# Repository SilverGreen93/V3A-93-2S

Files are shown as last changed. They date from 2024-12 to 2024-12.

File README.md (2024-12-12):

# Tramvaiul V3A-93-2S

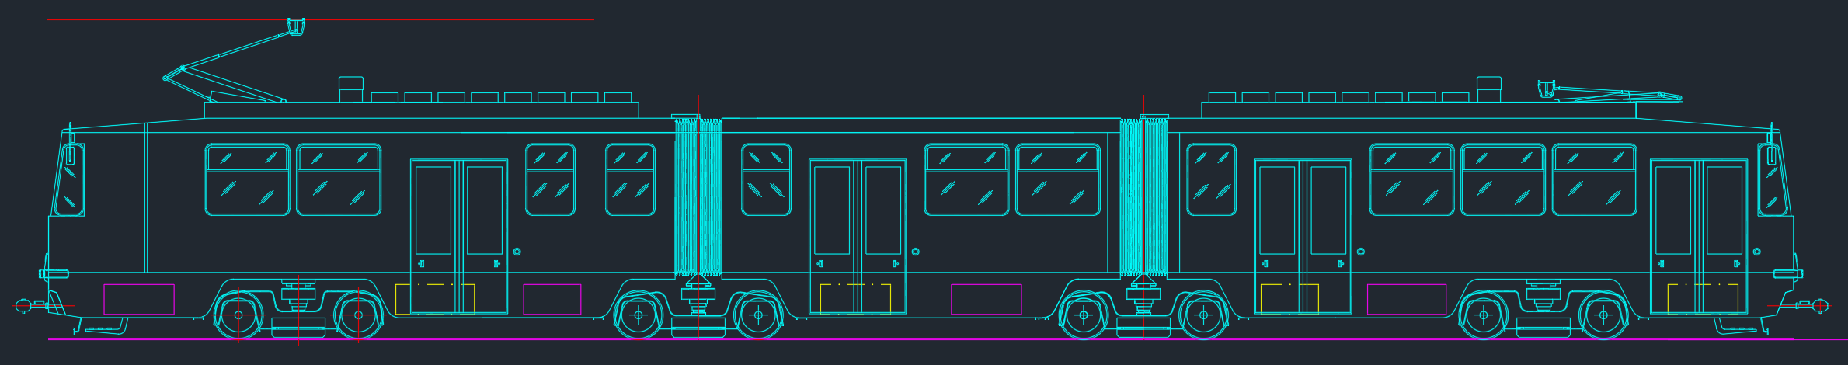
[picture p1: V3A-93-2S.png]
Diagramă V3A-93-2S


Acest repository conține schemele electrice ale tramvaiului românesc bucureștean bidirecțional V3A-93-2S, realizate la RATB - URAC (Regia Autonomă de Transport București - Uzinele de Reprarații Atelierele Centrale) în iulie 2006 de către inginerul proiectant Vasile Dănciulescu.

Schemele se prezintă în formatul original DWG (AutoCAD 2002), dar au fost convertite și în format DXF pentru a putea fi deschide în LibreCAD sau LibreOffice Draw.

De asemenea pentru o vizualizare pe orice dispozitiv sau posibilitate de imprimare imediată, le găsiți disponibile și în format portabil PDF.

# Structură

Găsiți împărțite pe dosare diferite schemele grupate din punct de vedere logic.

Punctul de pornire îl reprezintă dosarul [DOCUMENTATIE](DOCUMENTATIE) unde puteți consulta Memoriul de prezentare și Standardul de firmă (fișa tehnică detaliată a tramvaiului) în format document Word 2003 (original doc, convertit la docx).

Al doilea punct de interes esențial este dosarul [SCHEME](SCHEME), unde se prezintă schemele specifice fiecărui sistem electric al tramvaiului.

Diagrama tramvaiului și bordul cabinei de conducere sînt prezentate în dosarul [PANOURI APARATE](PANOURI%20APARATE).

# Mulțumiri

Mulțumesc pe această cale domnului inginer Vasile Dănciulescu pentru punerea la dispoziția mea pentru publicare aceste scheme ce conțin informații utile pentru istoria transportului bucureștean și oricărui pasionat care dorește răspunsuri tehnice la anumite subansamble ale tramvaielor produse la URAC.

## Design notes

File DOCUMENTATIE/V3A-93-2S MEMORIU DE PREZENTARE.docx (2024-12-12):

### RATB-URAC

### MEMORIU

### DE

### PREZENTARE

### VAGON DE TRAMVAI

### TIP V3A-93-2S

### IULIE 2006

### 1. DENUMIRE PRODUS

Vagon de tramvai articulat V3A-93-2S

### 2. DESCRIEREA PRODUSULUI

2.1 Generalităţi

Vagonul modernizat V3A-93-2S este rezultatul aplicării soluţiilor de modernizare de la proiectul V3A-93 adaptate la vagonul V3A-2S care este un vagon bidirecţional (cu două posturi de conducere şi uşi pe ambele părţi). Acest tip de vagon este necesar pentru deservirea traseelor care nu permit bucle de întoarcere la capete, sau pentru porţiuni de trasee aflate în construcţie.

Aspectul interior al salonului de pasageri a fost îmbunătăţit prin organizarea iluminatului fluorescent, îmbrăcămintea interioară a vagonului se realizează cu plăci care nu sunt higroscopice, rezistente la zgârâieturi, variaţii de temperatură, vibraţii mecanice, având o bună durabilitate.

Vagoanele sunt echipate cu scaune pentru călători montate în consolă şi realizate din materiale rezistente, cu proprietăţi antivandalism şi uşor lavabile.

Indicatoarele de traseu, uşor lizibile, uşurează informarea călătorilor, iar pentru comunicarea conducătorului de vehicul cu aceştia, este prevăzută o instalaşie de de anunţare automată.

Microclimatul vagonului este îmbunătăţit prin montarea pe tronsoanele A şi B a câte unui ventilator. Funcţionarea acestora este, funcţie de sensul de mers, cu introducerea aerului în vagon pe tronsonul A şi scoaterea acestuia pe tronsonul B. Salonul de pasageri este dotat cu elemente rezistive montate pe pereţiilaterali şi două aeroterme prevăzute cu termostat individual.

Uşile cu mişcare plan-paralelă, cu deschidere în exteriorul vagonului, determină o utilizare maximă a spaţiului din zona acceselor. Ele pot fi comandate direct de pasageri, iar automatizarea acestora asigură protecţia pasagerilor contra strângerii la închidere, în conformitate cu normativele internaţionale. Uşile sunt prevăzute cu geamuri lipite.

Pentru creşterea fiabilităţii în ansamblu s-au avut în vedere atât soluţii tehnice la subansamblele care au prezentat defecţiuni sistematice, mergându-se la reproiectare, cât şi măsuri tehnologice.

Din punct de vedere al caracteristicilor tehnice generale de siguranţa circulaţiei, vagonul V3A-93-2S se încadrează atât în condiţiile standardului de firmă cât şi în prevederile codului rutier.

2.2 Descrierea generală a vagonului

Vagonul de tramvai V3A-93-2S are la bază documentaţia de execuţie APUPS şi SPC-URAC.

Vagonul de tramvai V3A-93-2S este un vagon de tramvai dublu articulat format din trei tronsoane:
A – Tronsonul din faţă – cu cabina de conducere

C – Tronsonul din mijloc

B – Tronsonul din spate – cu cealaltă cabină de conducere

Vagonul de tramvai este echipat cu patru boghiuri, două boghiuri motoare şi două boghiuri purtătoare. Boghiurile purtătoare sunt dispuse sub articulaţiile vagonului. Caroseria vagonului se sprijină pe bighiuri prin intermediul rulmenţilor fixaţi pe traverse osclante,

Atât boghiurile motoare cât şi boghiurile purtătoare sunt de tip cu două osii, cu două trepte de suspensie şi cu patine electromagnetice.

Boghiurile motoare sunt prevăzute pe ambele osii cusisteme de frână disc, acţionate de dispozitive cu resort de acumulare.

Boghiul purtător dintre tronsoanele B şi C ale vagonului este prevăzut pe ambele osii cu sisteme de frână disc acţionate de un solenoid.

Boghiurile motoare au motorul de tracţiune dispus longitudinal, care antrenează două reductoare cu angrenaje conice flanşate pe scuturile acestuia. Întregul ansamblu motor-reductor este suspendat faţă de rama boghiului şi este cuplat cu osiile prin intermediul unor cuple cu elemente elastice.

Rama boghiului este de tip H construcţie cheson realizată din tablă OL44-2k asamblată prin sudură.

Trenurile de roţi folosesc roţi elastice. Osia montată este prevăzută cu disc de frână şi semicuplă pentru transmiterea momentului de tracţiune (la boghiurile motoare).

Contactul de punere la pământ este de tip radial. Carcasa contactului de punere la pământ se fixează pe cutia de unsoare.

Boghiurile sunt prevăzute cu două trepte de suspensie. Suspensia primară între osia montată şi rama boghiului este de tipul metal-cauciuc (arcuri Megy),

Pe cutia de unsoare mai sunt montate tampoane de cauciuc care preiau suprasarcinile accidentale.

Suspensia secundară este dispusă între rama boghiului şi traversa oscilantă şi este tot de tipul metal-cauciuc (arcuri Contitech).

Traversa oscilantăeste o construcţie metalică tip cheson executată din tablă OL44, asamblată prin sudură.

Patina electromagnetică de frână este montată suspendat pe cutia de unsoare pentru a asigura păstrarea distanţei între şină şi patină independent de flexiunea suspensiei primare a boghiului.

Vagonul de tramvai este prevăzut cu patru sisteme independente de frânare. Vagonul dispune de frână reostatică, frână cu patină la şină, frână cu solenoid, frână cu resort de acumulare.

Sistemele de frână sunt independente, astfel încât defectarea unuia nu se transmite şi celorlalte.

Frâna de serviciu (reostatică) acţionează numai asupra roţilor motoare. În circuitu frânei de serviciu nu există siguranţe electrice. Viteza minimă până la care frâna reostatică îşi păstreză eficacitatea este de 10 km/h. Simultan cu frâna reostatică, în cadrul frânării cu frâna de serviciu, funcţionează frîna cu solenoid. Frâna cu solenoid se montează pe boghiul purtător B-C şi este eficace tot până la viteza de 10 km/h.

Pentru oprirea vagonului la punct fix, sub viteza de 10 km/h, vor acţiona dispozitivele cu resort de acumulare, dispuse pe boghiurile motoare cu acţionare pe discurile de frână fixate pe osiile motoare. În cazul în care unul dintre dispozitivele cu resort de acumulare se defectează, acesta se poate izola cu ajutorul mecanismului montat pe boghiurile motoare pentru fiecare frână cu resort.

Pentru oprirea vagonului la punct fix se poate folosi şi frâna cu patină electromagnetică, la şină.

Frâna de staţionare compusă din dispozitivele cu resort de acumulare asigură staţionarea în rampă de 60‰ a vagonului încărcat cu 20 t.

Frâna cu patină la şină este independentă de aderenţa dintre roată şi şină, ea se aplică simultan cu frâna de serviciu. Frâna de urgenţă se realilează prin funcţionarea simultană a frânei de serviciu şi a frânei cu patină la şină.

Caroseria tronsoanelor vagonului de tramvai este de tipul semiautoprtantă, confecţionată din profile din oţel ambutisate, are învelişul exterior din tablă fixată în sudură pe schelet, participând în acest fel ca element de rezistenţă. Acoperişul vagonului este realizat din tablă sudată pe cintrele scheletului şi pe elementele de legătură ale acestora.

Pentru protecţia tamponării tronsoanele A şi B au fost protejate cu un blindaj frontal. Structura metalică a vagonului este protejată anticoroziv prin vopsire la exterior, iar la interior antifonic.

Postul de conducere al vagonului de tramvai are o uşă care separă postul de conducere de spaţiul ocupat de pasageri.

În cabina de conducere sunt amplasate: scaunul conducătorului de tramvai (prevăzut cu sistem de reglare pe verticală şi faţă-spate), panoul de aparate de bord, controlerul de mers-frână, dulapurile cu echipament electric situate în stânga şi în spate faţă de conducătorul tramvaiului, instalaţia de climatizare şi degivrare a parbrizului, ventilatorul amplasat deasupra scaunului conducătorului, oglinda interioară, radiatorul şi sursa de alimentare a acestuia, staţia de amplificare, pedala de salvare acţionată din cabină şi pedala de vigilenţă, microfonul aşezat pe pupitrul din partea reaptă, programatorul indicatorului de traseu şi difuzorul situate în spatele conducătorului tramvaiului.

Pe exteriorul cabinei se amplasează un ştergător de parbriz, iar pe laterale, două oglinzi retrovizoare amplasate stânga-dreapta, prevăzute cu încălzire.

Sistemul de organizare a postului de conducere asigură manipulantului un câmp de vizibilitate sub un unghi de 130 – 135°.

Organizarea întregii instalaţii electrice şi echipamentul electric al vagonului este următoarea:

- cabină manipulant, care cuprinde dulap panouri cu aparate, pupitrul de comandă cu aparatajul necesar conducerii şi supravegherii mersului, aeroterma pentru încălzirea cabinei, controlerul de mers-frână, pedala de vigilenţă, instalaţia de ventilaţie şi iluminat cabină, instalaţia de sonorizare, ventilator.
- salon, care cuprinde instalaţia de comandă uşi, rezistenţele de încălzire salon pasageri, aeroterme, instalaţia de iluminat salon.
- tronson A, B, C – exterior vagon care cuprinde cutiile de legături motoare ACM, BCM, alte cutii de legături, canalele de cabluri, compartimente aparate vagon A, compartimente aparate vagon B. Pe rama vagon A mai sunt amplasate cutia de rezistenţe punere la pământ, cutia de rezistenţe de preexcitare, iar pe vagonul C, compartimentul sursă statică, compartimentul acumulatori, rezistenţa punere la masă.
- vagon tronson A şi B: pe acoperişul acestora se amplasează pantografele, bateriile de rezistenţe demaraj-frânare, întrerupătorul automat, bobina self, descărcătorul cu rezistenţă variabilă.

2.3 Ansamblul postului de conducere

În cadrul postului de conducere se concentrează elementele de comandă şi control necesare pentru deplasarea în condiţii de deplină siguranţă şi funcţionalitate a vagonului de tramvai.

Postul de conducere este izolat de salonul de pasageri printr-o uşă, ceea ce rează condiţii mai bune pentru conducere.

Amplasarea elementelor de acţionare este ergonomică, în interiorul postului este asigurată o ventilaţie şi o încălzire corespunzătoare, indiferent de condiţiile meteorologice.

2.4 Instalaţia de încălzire şi degivrare post conducere

Pentru realizarea degivrării parbrizului, se foloseşte degivratorul din aeroterma post conducere. Comanda degivrării este realizată de manipulant printr-un buton amplasat pe pupitru.

Încălzirea postului de conducere se face printr-o aerotermă amplasată sub pupitru în partea dreaptă a manipulantului, care are o putere de 3 kW şi este alimentată la 750 Vcc. Comanda se face printr-un buton amplasat pe pupitru.

Aerul este aspirat din cabină printr-o mască şi este dirijat printr-o tubulatură şi gurile de refulare spre parbriz şi spre interiorul cabinei.

2.5 Sistemul de frânare

2.5.1 Generalităţi

Vagonul de tramvai V3A-93-2S este echipat cu patru sisteme de frânare, funcţionând pe principiul “totul electric” şi care asigură oprirea şi staţionarea vagonului în condiţii de deplină securitate pentru transportul urban.

Aceste sisteme permit frânarea normală (sau de serviciu) şi frânarea bruscă (sau de urgenţă).

Cele patru sisteme de frânare sunt:

- Frâna reostatică sau electrodinamică
- Frâna cu solenoid
- Frâna cu resort de acumulare
- Frâna electromagnetică la şină

2.5.2 Frâna reostatică

Frâna reostatică se comandă prin controler, trecând maneta acestuia în zona de frânare şi parcurgând în mod gradat, funcţie de necesităţi, cele 17 trepte de frânare. În aceste condiţii motoarele sunt alimentate pe primele 6 trepte din reţeaua de joasă tensiune în înfăşurările de excitaţie. Motoarele intră în regim de generatoare, debitând separat pe două reostate de frănare, deci o defecţiune pe un circuit nu afectează pe celălalt.

Frânarea reostatică este eficientă până la 10 km/h.

2.5.3 Frâna cu solenoid

După cum s-a arătat, frâna cu solenoid lucrează concomitent cu frâna reostatică, fiind complementară a acesteia.

Pe timpul staţionării, frâna cu solenoid poate fi utilizată ca o frână complementară frânei cu resort de acumulare.

Solenoidul se alimentează la 24 Vcc.

2.5.4 Frâna cu resort de acumulare

Frâna cu resort de acumulare se utilizează pentru oprirea la punct fix a vagonului şi ca frână de staţionare, deoarece forţa de frânare se realizează prin destinderea unor resorturi.

Dispozitivul resortului de acumulare permite pretensionarea hidraulică a acestuia. Comanda frânei se face prin evacuarea uleiului care realizează pretensionarea, iar forţa dezvoltată de resort se transmite prin intermediul unei timonerii de frână asupra saboţilor ce presează discul de frână.

Frânarea cu dispozitivele cu resort de acumulare se face fie prin intermediul controlerului, fie prin intermediul comutatorului de pe panoul de bord.

2.5.4 Frâna electromagnetică la şină

Toate sistemele de frâmă descrise depind de limita de aderenţă a roţilor pe calea de rulare. Prin intermediul patinelor electromagnetice la şină, greutatea vagonului este mărită cu cca. 35 t, având ca urmare un efect puternic de frânare.

Toate patinele sunt alimentate la 24 Vcc.

Datprită forţelor mari care se transmit asupra ghidajelor patinelor electromagnetice şi a supratensiunilor de comutaţie, nu se recomandă a se abuza de acest sistem de frânare, el trebuind să rămână un sistem de frână de urgenţă.

3. DOCUMENTAŢIA DE EXECUŢIE

La întocmirea tehnologiei de execuţie s-a ţinut cont de: organizarea fluxurilor tehnologice existente în URAC, de dotarea tehnică a liniilor tehnologice precum şi de structura organizatorică a atelierelor, astfel încât reperele executate să respecte condiţiile tehnice din documentaţia de execuţie.

4. CONDIŢII DE FUNCŢIONARE PRIVIND SECURITATEA, SĂNĂTATEA SAU CALITATEA VIEŢII PERSOANEI

4.1 Condiţii privind securitatea şi sănătatea persoanei

4.1.1 Rezistenţa electrică a legăturilor dintre părţile conductoare accesibile şi masă este mai mică de 5 mΩ.

4.1.2 Rezistenţa electrică dintre punctul de conectare la masă al instalaţiei de 750 V şi şină este mai mică de 5 mΩ.

4.1.3 Rezistenţele de izolaţie sunt mai mari de 10 MΩ în stare rece şi uscată şi mai mari de 2 MΩ în stare umedă.

4.1.4 Vagonul trebuie să reziste unei încercări a rigidităţii dielectrice a izolaţiilor conf. CEI77. Se încearcă rigiditatea dielectrică a izolaţiilor:

- Între circuitele de joasă tensiune şi masă – la 750 V,

- Între instalaţia de 750 V şi masă,

- Între instalaţia de 750 V şi circuitele de joasă tensiune – la 3875 V.

4.1.5 Supratemperaturile maxime admisibile după funcţionarea vagonului încărcat timp de 8 ore la principalele agregate, subansamble şi compartimente trebuie să fie:

- reductor de tracţiune 60°C

- lagăr cutie cap osie 55°C

- motor tracţiune TN71 – colector 65°C

- înfăşurare stator 115°C

- înfăşurare indus 80°C

- compartiment controler 50°C

- compartiment conexiune 30°C

- cabluri în jgheab 30°C

- dulapuri de aparataj 25°C

Vagonul va fi încărcat la 80% din sarcina maximă.

4.1.6 Materialele folosite la execuţia produsului trebuie să fie însoţite de certificate de conformitate şi garanţie emise de furnizor. Pentru principalele materiale utilizate la salonul de călători se vor solicita şi avizele privind comportarea la foc, precum şi cele referitoare la igiena şi protecţia muncii.

4.1.7 Trepte tuturor scărilor sunt acoperite cu material antiderapant.

4.1.8 Treptele fiecărei scări sunt iluminate dacă uşa respectivă este deschisă şi dacă sunt aprinse lanternele de poziţie.

4.1.9 Pe toată podeaua vagonului este lipit cu răsfrângere pe pereţii laterali un covor antiderapant.

4.1.10 Pe acoperişul tronsoanelor A şi B, pe ambele laterale, în dreptul rezistenţelor de frânare şi a întrerupătorului untrarapid, există pasarele acoperite ccu tablă striată de aluminiu.

4.1.11 Dacă vagonul nu staţionează, eliberarea pedalei de vigilenţă va declanşa automat frânarea vagonului.

4.1.12 Grătarul salvării cade pe şină dacă asupra declanşatorului frontal este aplicată o forţă normală dinspre exterior.

4.1.13 În salonul pasagerilor sunt amplasate cel puţin etichetele cu inscripţionări de securitate din tabelu 1.

Tabelul 1

Nr. crt. | Dimensiuni (mm) | Text | Poziţia de amplasare
1 | 200x45 | ÎN TIMPUL MERSULUI VĂ RUGĂM SĂ VĂ ŢINEŢI DE BARE | Pe mijloacele capacelor fixe
2 | 85x85 | ÎN CAZ DE PERICOL ROTIŢI MÂNERUL ÎN JOS ŞI DESCHIDEŢI MANUAL UŞA. ABUZUL SE PEDEPSEŞTE | Pe lateralul cutiilor cu aparataj ale uşilor, alături de mânerul de acţionare
3 | 200x100 | ÎN TIMPUL MERSULUI ESTE INTERZIS CĂLĂTORILOR SĂ STEA DE VORBĂ CU CONDUCĂTORUL VEHICULULUI | În spatele posturilor de conducere
4 | 80x50 | FRÂNĂ DE UTGENŢĂ. ABUZUL SE PEDEPSEŞTE | Pe lateralul cutiilor de aparataj ale uşilor, alături de butonul de acţionare
5 | 150x50 | NU VĂ SPRIJINIŢI DE UŞĂ. UŞA SE ÎNCHIDE AUTOMAT | Pe rama superioară a uşii, lizibil din interior
6 | 120x45 | FUMATU INTERZIS | În colţul geamurilor fixe, lizibil din interior
7 | 150x25 | NU VĂ SPRIJINIŢI DE ELEMENTELE ARTICULAŢIEI | Pe fiecare stâlp de articulaţie la înălţimea de 1800 mm
8 | 80x80 | fulger (semnul de indicare a pericolului de electrocutare) ATENŢIE 750 V ! | În centru capacelor izolante indicate

4.2 Condiţii privind calitatea vieţii persoanei

4.2.1 Materialul cu care se realizează îmbrăcămintea interioară a pereţilor şi a plafonului este sub formă de plăci cu următoarele caracteristici minimale:

- culoare uniformă

- rezistenţă la încovoiere prin şoc de min. 42 daN/cm²

- absorbţie apă de max. 0,13 %

- stabilitate dimensionalp până la min. +85°C

- ignifug

Îmbinarea plăcilor este mascată cu ajotorul unor profile de aluminiu.

4.2.2 Pe fiecare tronson, în salonul călătorilor, există rezistenţe de încălzire semiîngropate în pereţi şi acoperite cu capace de protecţie perforate din oţel inoxidabil. Rezistenţele încălzesc salonul dacă butonul “Încălzire salon” este apăsat.

4.2.3 În salonul pasagerilor şi în exteriorul vagonului sunt amplasate cel puţin etichetele cu inscripţionări de dirijare şi orientare din tabelul 2.

Tabelul 2

Nr. crt. | Dimensiuni (mm) | Text | Poziţia de amplasare
1 | 70x80 | DESCHIDERE UŞĂ APĂSAŢI BUTONUL | Pe axa verticală a butonului, deasupra acestuia la 15mm, atât în interior cât şi în exterior
2 | ø70 | Săgeată groasă cu vârful în jos | Pe geamurile uşilor atât în interior cât şi în exterior
3 | ø70 | Bară groasă orizontală | Pe geamurile uşilor atât în interior cât şi în exterior
4 | 160x20 | LOCURI REZERVATE | Pe peretele interior, la mijlocul intervalului dintre primele două scaune dinspre postul de conducere, la 15mm sub profilul de avial
5 | 120x80 | Săgeată groasă cu vârful în jos | La partea superioară a fiecărei bare pe care este montat un validator de tichete

4.2.4 Instalaţia de audioamplificare a vagonului care cuprinde un amplificator şi un microfon în postul de conducere şi o reţea de difuzoare montate în tavan, care trebuie să poată asigura un nivel sonor de cca. 60 dB(A).

5. MĂSURI DE PROTECŢIE A MUNCII ŞI A MEDIULUI

În procesul de fabricaţie al vagonului V3A-93-2S, sunt respectate următoarele norme:

- Instrucţiuni proprii de protecţia muncii pentru întreţinerea şi repararea tramvaielor şi troleibuzelor RATB-1997
- Norme specifice de securitate a muncii pentru construcţii şi confecţii metalice nr. 42/1999
- Norme specifice de securitate a muncii pentru prelucrarea metalelor prin aşchiere nr. 1/1997
- Norme specifice de securitate a muncii pentru sudarea şi tăierea metalelor nr. 1/1997
- Norme specifice de protecţia muncii pentru activităţi de vopsire nr. 26/1996.
- Legea protecţiei muncii nr. 90/1996 şi norme metodologice de aplicare
- Norme generale de protecţia muncii – 1996
- Norme specifice de protecţia muncii pentru transportul şi distribuţia energiei electrice nr. 65/1997
- Norme specifice de securitate a muncii pentru lucrul la înălţime nr. 12/1995
- Instrucţiuni de exploatare pentru proiectarea, construirea, montarea, exploatarea şi verificarea macaralelor, mecanismelor de ridicat şi dispozitivelor auxiliare “R1/1987”.

6. MONTARE, REGULI DE SECURITATE ŞI FOLOSIRE ÎN EXPLOATARE

În conformitate cu documentaţia de execuţie, în realizarea şi exploatarea produsului sunt îndeplinite:

- montarea este în conformitate cu documentaşia emisă de proiectant,
- securitatea şi utilizarea în exploatare au la bază:
  - protecţia călătorilor contra electrocutării şi atingerii instalaţiei electrice sub tensiune prin amplasarea echipamentului electric în compartimente speciale, protejate cu uşi şi capace prevăzute cu închizători,
  - protecţia contra incendiilor prin utilizarea de cablaje cu proprietăţi ignifuge şi realizarea instalaţiei de stins incendiu din compartimentele expuse incendiului,
  - asigurarea siguranţei circulaţiei prin menţinerea stării tehnice corespunzătoare, permanent a vagonului,
- Instrucţiunile de exploatare elaborate, conţin:
  - pregătirea vagonului pentru cursă,
  - pornirea vagonului şi conducerea acestuia în regim economic,
  - frânarea şi oprirea vagonului,
  - staţionarea vagonului,
  - defecte posibile şi modul de rezolvare în traseu,
  - remorcare tramvai defect,
  - măsuri pentru asigurarea siguranţei circulaţiei în situaţii speciale în exploatare,
  - măsuri de protecţia muncii şi PSI pentru conducătorul de tramvai.

MEMORIU DE PREZENTARE MP-V3A-93-2S Data intrării în vigoare 2006 VAGON DE TRAMVAI TIP V3A-93-2S Revizie finală Fila 11/11

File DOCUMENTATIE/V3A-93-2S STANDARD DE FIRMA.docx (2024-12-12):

APROBAT

DIRECTOR TEHNIC MATERIAL RULANT

ing. IORDACHE ŞTEFAN

### 1. GENERALITĂŢI

1.1 Obiectul standardului de firmă

1.1.1 Prezentul standard de firmă se referă la vagoanele de tramvai tip V3A-93-2S, respectiv vagoane cu doua sensuri, modernizate, destinate transportului urban de călători la suprafaţă şi subteran.

1.2 Domeniul de utilizare

Prevederile prezentului standard de firmă se aplică vagoanelor de tramvai tip V3A-93-2S având la bază documentaţia de execuţie RATB reactualizată de APUPS în colaborare cu SPC-URAC.

1.3 Documente de referinţă

- Norme de circulaţie pe drumurile publice;
- Regulamentul de exploatare tehnică a tramvaielor, Ordinul 92/1975-CPCP (RET);
- SR 13342:1996 Transport public urban de călători. Parametrii tehnici;
- BOStrab Bracking Regulations (Regulamentul de frânare BOStrab) 1988;
- Norme - Instrucţiuni tehnice departamentale pentru proiectarea şi construcţia liniilor de tramvai, cod PD164-82;
- CEI 77 Norme care se aplică aparatajului electric de tracţiune;
- STAS 9364/2-91 Vehicule rutiere. Ştergătoare de parbriz. Condiţii generale de calitate;
- STAS 6926/1-90 Autovehicule. Metode de încercare;
- SR ISO 3469:1995 Autoturisme. Sisteme de spălare a parbrizului. Metode de încercare;
- SR HD 405.1 S1:1993 Încercări ale cablurilor electrice supuse la foc. Partea 1: Încercare efectuată pe un cablu vertical;
- SR CEI 332-3:1993 Încercări ale cablurilor electrice supuse la foc. Partea 3: Încercări pe mănunchiuri de cabluri;
- Fişa UIC 564-2;
- STAS 9051/11-75 Suporturi textile acoperite cu elastomeri sau materiale plastice. Comportarea la flacără. Clasificare şi metode de încercare;
- STAS 12321-85 Materiale plastice. Determinarea combustibilităţii prin metoda indicelui de oxigen;
- DIN 51130D;
- STR 680-88-MTTc;
- STAS 6926/7-88 Vehicule rutiere. Etanşarea cabinei şi caroseriei la gaze şi apă. Metode de încercare;
- STAS 8393/5-81 Încercări climatice şi mecanice. Încercarea la căldură umedă ciclică, ciclul de 12+12 h. Metoda de încercare Db;
- STAS 7222-90 Acoperiri metalice. Acoperiri electrochimice de zinc sau cadmiu. Condiţii tehnice de calitate;
- STAS 7043/1-93 Acoperiri nemetalice (anorganice). Acoperiri prin oxidare anodică a aluminiului şi a aliajelor de aluminiu. Condiţii tehnice de calitate;
- STAS 2700/8-82 Organe de asamblare filetate. Caracteristici şi metode de verificare pentru acoperiri de protecţie;
- SR EN ISO 2178:1998 Acoperiri metalice. Determinarea grosimii stratului prin metoda magnetică;
- STAS 6854-90 Acoperiri metalice. Determinarea grosimii stratului prin metoda cu picături;
- Procese tehnologice RT1, RT2 pentru vagoanele modernizate V3-93, proiect SPC nr 3710-1996;
- SR ISO 2808:1993 Vopsele şi lacuri. Determinarea grosimii peliculei;
- SR CEI 60349:1999 Maşini electrice rotative pentru vehicule pe şine şi rutiere;
- CEI - 1133:1992 Traction electrique - Materiel roulant;
- STAS 2172/2-84 Piese de oţel forjate liber. Adaosuri de prelucrare şi abateri limită pentru piese forjate pe ciocane;
- SR ISO 8062/1995 Piese turnate. Sistem de toleranţe dimensionale şi adaosuri de prelucrare;
- STAS 8499/1987 Vehicule rutiere. Frânarea. Terminologie

1.4 Terminologie

In înţelesul prezentului standard de firmă, următoarele noţiuni au semnificaţiile:

1.4.1 Echipament de frânare - ansamblu de dispozitive de frânare care echipează un vehicul şi care are funcţia de a micşora sau de a anula viteza unui vehicul în mers, sau de a-l menţine imobil dacă este oprit.

1.4.2 Dispozitiv de frânare de serviciu - ansamblu de elemente care permit conducătorului să micşoreze, sau să anuleze, direct sau indirect, viteza unui vehicul în timpul conducerii sale normale. Acţiunea sa este variabilă.

1.4.3 Dispozitiv de frânare de securitate (de urgenţă) - ansamblu de elemente care permit conducătorului să micşoreze, sau să anuleze, direct sau indirect, viteza unui vehicul,suplimentar frânei de serviciu si independent de aderenta roata-sina in cazul materialului rulant. Acţiunea sa este variabilă.

1.4.4 Dispozitiv de frânare de staţionare - ansamblu de elemente care permit menţinerea în mod mecanic a unui vehicul imobil, chiar pe un teren înclinat sau în absenţa conducătorului.

1.4.5 Frânare de serviciu - frânarea până la viteza dorită sau până la oprirea vagonului fără punerea în pericol a ocupanţilor vehiculului (conform "Regulamentului de frânare BOStrab).

1.4.6 Frânare de urgenţă - frânare comandată de către conducător dacă apare un pericol în afara vagonului; frânarea poate duce până la oprire; în timpul frânării apar deceleraţii crescute şi smucituri;

1.4.7 Frânare de staţionare - frânare utilizată pentru prevenirea plecării de pe loc a vehiculului (conform "Regulamentului de frânare BOStrab).

1.4.8 Iluminatul normal - funcţionarea iluminatului salonului cu tuburi fluorescente alimentate din tensiunea furnizată de sursă în tampon cu bateria de acumulatori la tensiunea de 24 V.c.c. ±20%.

1.4.9 Iluminatul de siguranţă - funcţionarea iluminatului din bateria de acumulatori de 24 V.c.c. cu becuri incandescente în cazul lipsei tensiunii furnizate de sursa statică

1.4.10 Circuite de joasă tensiune - circuite cu tensiunea nominală de alimentare 24 V.c.c.

1.4.11 Circuite de înaltă tensiune - circuite cu tensiunea nominală de alimentare de 750 V.c.c.

1.4.12 Fază scurtă - lumină de întâlnire

1.4.13 Fază lungă - lumină de drum. Este semnalizată şi la bord (bec martor).

Faza scurtă şi faza lungă sunt condiţionate de aprinderea prealabilă a luminilor de poziţie şi lămpilor de gabarit.

1.4.14 Indicele calităţii de mers - indice de evaluare a confortului călătorilor determinat de componenta dinamică a vehiculului pe cale. Formula determinată experimental a indicelui calităţii de mers este:

Wz =

în care:

Wz - indicele calităţii de mers

T - durata înregistrării valorilor acceleraţiei vibraţiilor

a = a(ν,t) este acceleraţia vibraţiilor în domeniul de frecvenţe (νmin , νmax);

B = B(ν) este un factor de ponderare în frecvenţă pentru acceleraţii, dependent şi de direcţia vibraţiilor.

1.4.15 Mers normal - cu ambele motoare de tracţiune în funcţiune. El se realizeaza în ambele sensuri de mers din posturi de conducere distincte şi pe echipamente şi circuite de tracţiune diferite pentru fiecare sens, cu exceptia motoarelor de tracţiune care sunt aceleaşi. Uşile de acces de pe fiecare parte laterală dreapta pot fi acţionate numai din postul de conducere corespunzător sensului respectiv de mers.

1.4.16 Mers de avarie - cu un motor de tracţiune defect izolat.

Atât mersul normal cat şi cel de avarie nu pot fi acţionate dintr-un post de conducere decât cu condiţia punerii axului inversor al controlerului din celălalt post pe pozitia ZERO şi după asigurarea celorlalte condiţii de mers: inchiderea uşilor, apăsarea pedalei de vigilenţă şi defrânarea vagonului din toate sistemele de frână. Frânarea, deschiderea uşilor, eliberarea pedalei de vigilenţă şi căderea tensiunii din reţea au prioritate în regimul de mers, în sensul că suprimă automat regimul de tracţiune. Tracţiunea nu poate fi reluată decât după readucerea controlerului (axul principal mers-frână) pe poziţia ZERO şi refacerea celorlalte condiţii de mers.

1.4.17 Exploatarea normală - în conformitate cu "Regulamentul de exploatare tehnică a tramvaielor" aprobat de CPCP.

1.4.18 Frâna cu patină la şină – sistem care asigură frânarea independent de coeficientul de frecare dintre roată şi şină.

1.4.19 Frâna cu solenoid – asigură frânarea vagonului simultan cu frânarea reostatică (realizată de motoarele de tracţiune numai pe boghiurile motoare) şi acţionează pe boghiul purtător BC. Ea se poate alimenta şi independent din sursa de joasă tensiune.

1.4.20 Grătarul salvării – este un subansamblu al dispozitivului de salvare care este declanşat şi cade la nivelul şinei în momentul atingerii declanşatorului de către un obstacol mai înalt de 140 mm şi care nu permite preluarea acestuia direct de agregatele de rulare.

1.4.21 Declanşatorul frontal al salvării – este un subansamblu al dispozitivului de salvare care la atingerea unui obstacol mai mare de 140 mm aflat între şine declanşează grătarul salvării, care cade la nivelul şinei.

1.4.22 Supratemperatură - prin supratemperatură se va înţelege diferenţa de temperatură între temperatura măsurată şi temperatura mediului ambiant;

1.4.23 Stare caldă - este starea echipamentului electric după două ore de funcţionare corectă (fără incidente, anomalii, etc.);

1.4.24 Post de conducere - este locul din care se face conducerea vehiculului şi se află în partea din faţa a tramvaiului asociată sensului de mers înainte.

1.5 Simbolizare

Vagonul de tramvai dublu articulat, format din 3 tronsoane, este simbolizat prin V3A-93-2S cu următoarele semnificaţii:

- V – vagon
- 3 – nr. tronsoane
- A – articulat
- 93 – varianta constructivă (modernizată)
- 2S – doua sensuri

1.6 Durata de viaţă

Conform Legii 15/1994 durata de utilizare normată este de 14 ani.

1.7 Cerinţe privitoare la mediul înconjurător

- Zona climatică: N (SR HD 478.2.1 S1:2002);
- Categoria de exploatare: 1 (STAS 6692-83);
- Domeniul temperaturilor de utilizare: -33...+55 oC;
- Umiditatea relativă medie lunară în perioada cea mai caldă şi umedă raportată la +20 oC: 90% timp de două luni;
- Altitudinea maximă de utilizare: 1200 m;
- Viteza maximă a vântului: 140 km/h;
- Atmosferă neexplozivă;
- Agenţi exteriori: ploaie, ceaţă, praf, noroi, zăpadă, chiciură, gheaţă, soluţie salină;
- Înălţimea maximă a apei peste nivelul superior al şinei: 50 mm;

1.8 Cerinţe constructive, funcţionale şi de altă natură

1.8.1 Cerinţe constructive

Cotele de gabarit şi funcţionale ale vagonului V3A-93 sunt reprezentate în anexa 1.

1.8.2 Cerinţe funcţionale

Vagoanele de tramvai sunt destinate să funcţioneze:

- în traficul urban
- viteza maximă 55 km/h
- raza minimă de înscriere în curbă 18 m
- aliniament obligatoriu în curbe S cu raza de 18 m 7 m
- raza curbei S fără aliniament 30 m
- raza minimă de mers în covată 800 m
- raza minimă de mers pe cocoaşă 800 m
- calea de rulare şi reţeaua de contact trebuie să fie executate conform “Normelor – Instrucţiuni tehnice departamentale pentru proiectarea şi construcţia liniilor de tramvai” cod PD 164 – 82, pentru a fi asigurate condiţiile de siguranţă a circulaţiei
- în vagoane formate din 3 tronsoane articulate
- rampa maximă 60 ‰
- ecartament linie: 1435 mm;
- Valorile maxime ale acceleraţiilor vibraţiilor determinate de calea de rulare:

- 8 g pentru capul osiei;

- 1 g pentru caroserie;

- 3 g pentru rama boghiului;

- 2 g pentru motorul electric de tracţiune;

- Tensiunea reţelei de contact: 750 Vcc.

1.9 Descrierea şi funcţionarea produsului

1.9.1 Vagoanele de tramvai sunt realizate din 3 tronsoane legate între ele, notate în ordinea:

A – tronsonul din faţă – cu cabina conducătorului de tramvai

B – tronsonul din spate – cu cealaltă cabină de conducere.

C – tronsonul din mijloc

Zona articulaţiei dintre două tronsoane este alcătuită din jug, podea de articulaţie, burdufuri, articulaţiile propriu-zise şi amenajarea interioară de protecţie pentru călători. Tronsoanele sunt asigurate împotriva desprinderii în situaţii de deraiere.

1.9.2 Caroseria tronsoanelor este de tipul semiautoportantă, confecţionată din profile de oţel, învelite cu tablă fixată prin sudură, care participă ca element de rezistenţă.

Acoperişul este realizat din elemente de legătură longitudinale şi transversale pe care se sudează tablă. Pentru protecţia la tamponări, tronsoanele A şi B au fost protejate cu un blindaj frontal.

1.9.3 Caroseria vagoanelor este protejată anticoroziv prin grunduire, vopsire şi antifonare.

1.9.4 Vagonul dublu articulat V3A-93-2S este echipat cu 4 boghiuri, dintre care 2 motoare şi 2 purtătoare. Boghiurile purtătoare sunt dispuse sub articulaţii. Boghiurile sunt prevăzute cu două tipuri de suspensie. Suspensia primară între osia montată şi rama boghiului şi suspensia secundară între rama boghiului şi caroseria vagonului. Suspensia primară este realizată cu resorturi de cauciuc tip MEGY iar suspensia secundară este cu resort de cauciuc tip Contitech.

Rama boghiurilor este de tip H construcţie cheson realizată din tablă OL44 2k asamblată prin sudură.

Fiecare boghiu motor este echipat cu un motor de tracţiune aşezat longitudinal faţă de sensul de deplasare al vagonului, acţionând prin intermediul a două reductoare asupra celor două osii şi de aici asupra roţilor elastice. Transmisia între reductor şi osie se realizează printr-un cuplaj elastic.

Legătura dintre boghiu şi caroserie se realizează prin intermediul unei traverse cu rulment de crapodină.

1.9.5 Vagoanele de tramvai sunt prevăzute cu 4 sisteme independente de frânare. Vagonul dispune de frână reostatică, frână cu patină la şină, frână cu solenoid şi frână cu resort de acumulare.

Frânele vagonului asigură oprirea în limitele şi condiţiile cuprinse la cap. 2. Sistemele de frânare sunt independente, încât defectarea unuia nu se transmite şi la celelalte. Frâna reostatică acţionează numai asupra roţilor motoare şi asigură o frânare la limita blocării roţilor. Forţa de frânare este realizată în trepte de frânare prin intermediul controlerului de bord. În circuitul frânei de serviciu nu există siguranţe electrice.

Viteza minimă până la care frâna reostatică îşi păstrează eficacitatea este de cca. 10 km/h.

Simultan cu frânarea reostatică, în cadrul frânării cu frâna de serviciu funcţionează frâna cu solenoid. Frâna cu solenoid este eficace tot până la viteza de circa 10 km/h. Pentru oprirea vagonului la punct fix sub viteza de 10 km/h se acţionează dispozitivele cu resort de acumulare dispuse pe boghiurile motoare cu acţionare pe discurile de frână fixate pe osiile motoare şi în plus se poate folosi şi frâna cu patină electromagnetică la şină.

Frâna de staţionare compusă din sistem cu resort de acumulare cu acţionare hidraulică HK asigură staţionarea în rampa de 60 ⁰/00 a vagonului încărcat cu 20 t.

Frâna cu patină la şină este independentă de aderenţa dintre roată şi şină. Ea se poate aplica simultan cu frâna de serviciu.

Frâna de urgenţă se realizează prin funcţionarea simultană a frânei de serviciu şi a frânei cu patină la şină.

1.9.6 Echipamentul electric de pe vagon se împarte în:

- Echipament electric de “înaltă tensiune”, valoarea nominală a înaltei tensiuni fiind 750 V.c.c.

- Echipament electric de “joasă tensiune”, valoarea nominală a joasei tensiuni fiind 24 V.c.c. ±20%

###### 1.9.6.1 Instalaţiile şi echipamentele electrice sunt protejate împotriva scurtcircuitelor, suprasarcinilor şi supratensiunilor accidentale, exceptând cazul frânării reostatice.

###### 1.9.6.2 În conformitate cu normele de circulaţie pe drumurile publice în vigoare, vagoanele de tramvai sunt dotate cu echipamente de iluminat, semnalizare de direcţie, semnalizare acustică, mers înapoi, stop şi altele.

###### 1.9.6.3 Iluminatul interior este asigurat de 26 tuburi fluorescente de 20 W alimentate prin invertoare electronice din sursa de joasă tensiune. Vizibilitatea pe timpul nopţii a conducătorului de vehicul nu este afectată de iluminatul interior.

###### 1.9.6.4 Fiecare casă a scării are amplasate lămpi prevăzute cu becuri de 24 V care se aprind la deschiderea uşilor în perioada când funcţionează lumina de poziţie.

###### 1.9.6.5 Instalaţia de comunicare

###### Vagonul dispune de cate o instalaţie de audioamplificare pentru informarea şi dirijarea călătorilor, din fiecare post de conducere, având câte 5 difuzoare în salon (1/A;2/C;2/B pentru un sens şi 2/A;2/C;1/B pentru celălalt sens) şi câte unul în cabină.

1.9.6.6 Vagonul este dotat cu cate 2 faruri rotunde ELBA prevăzute cu câte un bec de 40 x 45 W, pentru fază scurtă şi respectiv fază lungă şi cu câte un bec de 3 W pentru poziţie, pentru fiecare sens de mers. Pe colţurile părţilor frontale, stânga şi dreapta sunt montate câte 2 semnalizatoare de direcţie, tip A 3 – ELBA cu lumină portocalie, dotată cu un bec de 5 W.

###### Pe tronsoanele A şi B sunt montate, pe părţile laterale, câte două lămpi de semnalizare cu lumină intermitentă portocalie tip LDS, prevăzute cu becuri de 15 W, acţionarea acestora se face prin intermediul unui releu de semnalizare electronic.

Tronsoanele A si B au prevăzute, sub faruri, cate 10 lămpi tip AS1 prevăzute cu dispersor roşu pentru stop, poziţii pe ceaţă cu dispersor alb pentru mersul înapoi, dispersor galben pentru semnalizare direcţie şi avarie, cosiderate ca’ ”lampi spate” pentru fiecare sens de mers. Acestea, ca şi farurile, nu pot fi aprinse dacât conform codului de semnalizare rutieră din postul de conducere corespunzator.

###### Becul pentru stop este de 21 W, cel pentru poziţii şi semnalizare de 10 W, iar cel pentru mers înapoi şi ceaţă este de 15 W.

###### 1.9.6.7 Vagonul este prevăzut cu câte un clopot de semnalizare acustică cu acţionare electrică, pentru fiecare post de conducere. Intensitatea sonoră a clopotului este cuprinsă între 80÷90 dB măsurată în exterior.

###### 1.9.6.8 Protecţia împotriva supratensiunilor atmosferice este realizată cu cate un descărcător catodic cu rezistenţă variabilă, pentru fiecare echipament de tracţiune.

###### Circuitele electrice sunt protejate contra supracurenţilor şi suprasarcinilor prin siguranţe fuzibile sau întrerupătoare automate.

###### Circuitul motoarelor de tracţiune este protejat de câte un întrerupător automat pentru fiecare echipament de tracţiune. Rezistenţa de izolaţie între circuite şi masă este mai mare de 10 MΩ în stare rece şi uscată.

###### 1.9.6.9. Acţionarea vagonului se face cu două motoare de tracţiune de curent continuu. Comanda demarajului şi a frânării de serviciu se face cu ajutorul unui controler acţionat manual din fiecare post de conducere.

###### Regimul de mers normal este cu ambele motoare de tracţiune. În caz de defect se permite funcţionarea temporară cu un singur motor, prin izolarea motorului defect din maneta de comandă a axului inversor al controlerului.

Poziţiile manetei de comandă a axului inversor a controlerului sunt:

- mers înainte motor II
- mers înainte motor I
- mers înainte motor I + II
- zero (repaus)
- mers înapoi motor I + II
- mers înapoi motor I
- mers înapoi motor II

1.9.7 Tronsoanele A si B ale vagonului dispun de câte o cabină a conducătorului de vehicul care este de tipul complet închisă cu uşa de acces în dreptul primei semifoi a uşilor de acces în tramvai. În cabină sunt amplasate: scaunul, prevăzut cu un sistem de reglare pe verticală şi în adâncime – faţă de panoul de aparate al bordului; dulapurile cu echipament electric, situate în stânga şi în spate faţă de conducător; instalaţia de încălzire, ventilaţie şi degivrare a parbrizului.

###### Panoul cu aparate al bordului este prevăzut înclinat la 15° pentru ca razele reflectate să nu jeneze conducătorul.

###### Cabina de conducere este prevăzută cu un parbriz frontal care asigură o vizibilitate a conducătorului cu un unghi de 130 ÷ 135°. Pe parbriz şi geamurile laterale ale postului de conducere este aplicată folie bruxafol. Cabina este dotată cu un ştergător de parbriz şi instalaţie de spălare a acestuia.

###### Cabina are două oglinzi retrovizoare montate în exterior, în dreapta şi în stânga vehiculului, în direcţia de mers, prevăzute cu sistem de încălzire.

###### 1.9.8 Îmbrăcămintea interioară a pereţilor vagoanelor se realizează cu plăci care nu sunt higroscopice, sunt lavabile, rezistente la zgârâeturi, variaţii de temperatură, vibraţii mecanice, având o bună durabilitate în timp. Îmbinarea se face cu profile corespunzătoare fixate de caroserie.

1.9.9 Podeaua este realizată din plăci din material lemnos, impregnate pentru a nu fi higroscopice, aşezate pe şasiu prin intermediul unor cusaci de lemn şi benzi de cauciuc. In salon, pe podea, se amplasează prin lipire un covor de pardoseală realizat din materiale antiuzură, cu proprietăţi ignifuge conform normelor PSI în vigoare.

###### 1.9.10 Vagoanele sunt echipate cu scaune pentru călători, montate în consolă şi realizate din materiale rezistente, cu proprietăţi antivandalism şi uşor lavabile.

###### 1.9.11 În interiorul vagonului de pasageri sunt dispuse pe cele două părţi, bare de susţinere orizontale, amplasate la 1850 mm faţă de nivelul podelei vagonului. Ele sunt confecţionate din ţeavă de oţel, acoperite prin vopsire în câmp electrostatic.

###### 1.9.12 În scopul îndrumării călătorilor, vagoanele sunt prevăzute cu inscripţii indicatoare şi cu difuzoare şi instalaţie de anunţare automată a staţiilor acţionată de conducătorul vehiculului.

În partea exterioară a vagonului se înscriu:

- semne pe uşi cu indicaţia de urcare şi coborâre
- semne pentru marcarea locurilor de defrânare manuală

În partea interioară a vagonului se înscriu:

- locurile destinate pentru invalizi, femei gravide, persoane cu copii în braţe
- alte indicaţii cu privire la comportarea călătorilor
- geamurile folosite ca ieşire de urgenţă în caz de accident.

Pentru spargerea acestor geamuri, vagoanele sunt prevăzute cu ciocane fixate în suporţi şi sigilate.

Inscripţiile trebuie să fie vizibile şi lizibile.

1.9.13 Microclimatul vagonului este asigurat prin următoarele mijloace:

- ventilaţie naturală – ferestre rabatabile; ventilaţii centrale pe acoperiş – una tronsonul A şi una pe tronsonul B;
- ventilaţie forţată – câte un electroventilator pe tronsoanele A şi B care introduc aer în interior.
- Fiecare cabina manipulant este dotată cu aerotermă, ventilator în plafon şi radiator.
- salonul pasageri este dotat cu 12 elemente rezistive montate în pereţii laterali si 2 aeroterme (1/A si 1/B).
- microclimatul din interiorul vagonului este supravegheat prin instalarea unui termostat general.

###### 1.9.14 Pentru îmbunătăţirea aderenţei dintre roată şi cale, vagoanele sunt echipate cu cate 2 nisipare, instalate înaintea primei osii motoare pentru fiecare sens de mers şi pot fi acţionate numai câte doua din fiecare cabină, corespunzator sensului de mers inainte.

###### Nisiparele sunt dotate cu rezistenţe de încălzire şi uscare a nisipului, alimentate la 750 V printr-un circuit separat, protejat cu siguranţă fuzibilă.

###### Comanda nisipării se poate face atât automat simultan cu sistemele frânei de urgenţă, cât şi manual de către manipulant, separat de sistemele de frânare, pentru a se putea realiza demarajul în rampă.

###### 1.9.15 Vagoanele sunt prevăzute sub fiecare cabina a conducătorului cu un dispozitiv de salvare.

###### Salvarea este prevăzută cu un declanşator frontal şi un grătar. În timpul mersului, dacă vagonul şi respectiv declanşatorul frontal atinge un obstacol se declanşează grătarul pentru ca obstacolul să nu poată ajunge sub agregatele de rulare ale vagonului.

Declanşarea salvării se poate realiza şi de conducătorul vehiculului.

###### 1.9.16 Vagoanele au la capete câte un aparat de cuplare.

###### 1.9.17 Pentru identificarea numărului şi a traseului vagoanelor, tramvaiele sunt dotate cu indicatoare de traseu cu LED-uri comandate de cate un controler şi microprocesor instalat în cabinele de conducere:

- unul frontal şi două laterale, care indică traseul şi linia pe care circula, pentru fiecare sens de mers.

###### 1.9.18 Vagoanele au în dotare 6 stingătoare de incendiu cu praf şi CO2, accesibile conducătorului de vehicul, cât şi pasagerilor:

- cate un stingător deserveşte în mod permanent controlerul. Controlerul este prevăzut cu clapete de acces stingător gravitaţionale;
- cate un stingător deserveşte în mod permanent canalul de coborâre cabluri, fiind conectat la acesta prin ţeavă;
- două libere.

1.9.19 Pe acoperişul tronsoanelor A si B, în dreptul boghiurilor motoare este montat cate un pantograf, destinat să asigure captarea curentului de la reţeaua aeriană de contact, şi prevăzut cu înzăvorâre în poziţia coborât pentru fiecare sens de mers. Pantografele sunt de tip asimetric şi sunt utilizate alternativ (numai cel din fata, pentru fiecare sens de mers, celalalt fiind pliat).

###### De asemenea, pe acoperisul tronsoanelor A si B sunt montate câte un set de baterii de rezistente demaraj-franare şi câte un disjunctor cod 5500.

###### 1.9.20 Pentru accesul şi deplasarea personalului de intervenţie, pe acoperişul vagonului s-au prevăzut pasarele de tablă de aluminiu striată.

###### 1.9.21 Vagoanele sunt dotate cu semnale de alarmă la fiecare uşă care comandă frânarea vehiculului prin patine şi solenoid în caz de acţionare, precum şi activarea clopotului.

###### 1.9.22 Vagoanele sunt prevăzute cu instalaţii de siguranţă a circulaţiei şi vigilenţă (pedală de vigilenţă în fiecare cabină). Aceasta, în cazul pierderii capacităţii conducătorului şi neapăsarea pedalei, acţionează frâna de urgenţă a vagonului;

###### 1.9.23 Postul de conducere de pe tronsonul B elimină postul de manevra.

###### 1.9.24 Accesul călătorilor este asigurat prin uşile tip IFE de pe partea dreapta pentru fiecare sens de mers, dispuse astfel:

- tronson A – 2 uşi/dreapta + 1 uşă/stânga
- tronson B – 1 uşă/dreapta + 2 uşi/stânga
- tronson C – 1 uşă/dreapta + 1 uşă/stânga

Uşile 2, 3, şi 4, pentru urcarea pasagerilor, asigură o deschidere de aprox. 1200 mm. Fiecare din cele 4 uşi/sens sunt comandate din cabina conducătorului vagonului, pentru fiecare existând şi un buton de deschidere de către pasageri, atât pe interior cât şi pe exteriorul vehiculului, condiţionat de comanda conducătorul vehiculului. Uşa nr. 1/sens, semifoaia 1, este dotată cu buton de acţionare închidere exterior mascat. Această semifoaie este acţionată separat de celelalte uşi, fiind destinată numai accesului conducătorului de vehicul.

###### 1.9.25 Elementele interioare demontabile ale vagonului şi capacele compartimentelor cu aparate sunt asigurate, încât nu pot fi desfăcute decât de personalul de întreţinere şi de intervenţie. Pe panourile care conţin aparate cu pericol de electrocutare este marcat semnul de tensiune periculoasă.

###### 1.9.26 Principalele caracteristici tehnice şi funcţionale ale vagonului:

- ecartament 1435 mm
- raport de transmisie reductor 1:5,66
- formula osiilor B’2’2’B’
- masa vagonului gol 36,5 t +5%
- masa vagonului încărcat – maxim 53,1 t +5%

(Încărcătura utilă maximă se stabileşte ca fiind 750N/loc pe scaun + 5000N/m² de suprafaţă locuri în picioare – conform BOSTRAB. Aceasta este: Gu=34x750N+27,3m²x5000N=16200daN sau Gu=16510 kgf=16,51 tf.)

- nr. locuri - pe scaune 34
- în total călători 254 (65kg/călător)
- raza minimă de înscriere în curbă 18 m
- aliniament obligatoriu în curbe S cu raza de 18 m - minim 7 m
- raza curbei S fără aliniament minim 30 m
- raza minimă la mersul pe cocoaşă 800 m
- raza minimă la mersul în covată 800 m
- tensiunea de alimentare 750 Vcc
- puterea uniorară specifică 0,87 kW/kN
- acţionare vagon controler
- sisteme de frânare:

a. frână de serviciu -electrodinamică, frână cu resort cu solenoid

b. frână independentă de aderenţa roată–şină, - cu patină la şină

c. frână de staţionare - dispozitive cu resort de

acumulare cu acţionare hidraulică tip HK

- rampa maximă 60 ⁰/00
- viteza maximă 55 km/h
- acceleraţie demaraj 0,8 m/s²
- consum specific de energie fără încălzire cca. 8 Wh/kN km
- lungimea vagonului 27180 mm
- lăţimea vagonului cu uşile închise la înălţimea

de 3,4 m de la şină 2390 mm

- înălţime măsurată de la suprafaţa superioară a şinei la

suprafaţa de contact a pantografului retras 4200 mm

- putere nominală pentru tracţiune 2x120 kW

2. CONDIŢII TEHNICE

2.1 Condiţii de execuţie a reperelor

###### 2.1.1 Materialele, componentele şi subansamblurile utilizate trebuie să fie cele prevăzute în documentaţia de execuţie. Se permite utilizarea unor materiale, componente sau subansambluri cu caracteristici similare sau superioare, cu avizul scris al proiectantului şi beneficiarului.

2.1.2 Materialele folosite la execuţia produsului trebuie să fie însoţite de certificate de conformitate şi garanţie emise de furnizor. Pentru principalele materiale utilizate la salonul de călători se vor solicita şi avizele privind comportarea la foc, precum şi cele referitoare la igiena şi protecţia muncii.

###### 2.1.3 Derogările de la materialele indicate în documentaţie, se acordă pe bază de aviz scris emis numai de către proiectant la solicitarea scrisă a executantului cu avizul beneficiarului conform procedurii derogatorii.

###### 2.1.4 Pentru toate dimensiunile şi cotele neprevăzute cu toleranţe se respectă prevederile SR EN 22768/1:2, clasa de precizie m la toleranţele dimensionale şi s la toleranţele geometrice.

###### 2.1.5 Pentru toate dimensiunile şi cotele neprevăzute cu toleranţe, la piesele executate prin sudare, se vor respecta prevederile STAS 9101/1-89, clasa de precizie B.

###### 2.1.6 Pentru toate dimensiunile şi cotele neprevăzute cu toleranţe, la piesele executate prin turnare şi forjare se admit abateri limită conform STAS 2171/2-84 (piese forjate) şi respectiv SR ISO 8062/1995 (piese turnate).

###### 2.1.7 Derogările de la cotele şi toleranţele indicate în documentaţie se acordă în scris numai de către proiectant.

###### 2.1.8 Pregătirea pieselor pentru sudare şi operaţia de sudare trebuie să se facă în conformitate cu prescripţiile din documentaţia de execuţie.

###### 2.1.9 Echipamentul, agregatele şi componentele ce se achiziţionează, trebuie să fie omologate, în producţia curentă a furnizorului şi însoţite de certificate de conformitate şi garanţie şi avizele privind normele PSI, NPSM şi medicina muncii.

###### 2.1.10 Subansamblurile importante nominalizate în anexa 4 au standarde de firmă sau NTR, la livrare sunt însoţite de fişe de măsurători şi documente de atestare a calităţii conform contractului.

2.2 Condiţii de gabarit

- lungimea la gabaritul cu tampoane montate
- în axul longitudinal al vagonului 27180±150 mm
- lungimea la gabaritul fără tampoane 26180±30mm
- lăţimea măsurată la 1,4 m peste nivelul şinei 2390 ±10 mm
- înălţimea măsurată de la suprafaţa superioară a şinei la suprafaţa de contact a pantografului retras 4200 ±15 mm
- înălţimea salonului de pasageri 2220 ±10 mm
- distanţa între axul căii de rulare şi
- extremităţile oglinzilor retrovizoare 1400 ±10 mm
- garda la sol în stare nouă:

- vagon plin 140 ±10 mm

- vagon gol 160 ±10 mm

- garda la sol cu bandajele uzate la maximum

şi suspensia cu săgeata maximă:

- vagon plin 72 ±10 mm

- vagon gol 92 ±10 mm

- înălţimea în dreptul grătarului salvării (cu posibilitate de reglaj): - vagon plin 140 ±10 mm

- vagon gol 160 ±10 mm

2.3 Condiţii de greutate

###### 2.3.1 Greutatea unui vagon de tramvai gol este de 365 ± 5% kN şi condiţiile pentru încărcările pentru fiecare roată trebuie să corespundă tabelului din ANEXA 6.

###### 2.3.2 Valorile de încărcare a boghiurilor pentru vagonul de tramvai gol sunt: boghiu motor I 11800 daN ±5%

boghiu purtător AC 6450 daN ±5%

boghiu purtător BC 6450 daN ±5%

boghiu motor II 11800 daN ±5%

2.4 Condiţii privind calitatea suspensiei

###### 2.4.1 Vagonul în stare neîncărcată, după reglarea suspensiei traversei oscilante, trebuie să realizeze cota de 870 ± 10 mm între suprafaţa inferioară a structurii metalice a bazei caroseriei şi suprafaţa de rulare, stânga şi dreapta.

###### 2.4.2 În aceleaşi condiţii de la pct. 2.4.1 vagonul trebuie să realizeze pe lungimea sa cota de 870 ± 10 mm (faţă, spate, mijloc).

###### 2.4.3 Vagonul încărcat cu sarcina nominală trebuie să realizeze cota de 850 ± 15 mm între suprafaţa inferioară a bazei vagonului şi suprafaţa de rulare stânga şi dreapta cât şi pe lungimea sa (faţă, spate, mijloc).

    2.4.4 Distanţa dintre cadrul boghiului şi cutia de unsoare, respectiv cota “I”, este:

108 mm – vagon gol

96 mm – vagon încărcat

2.5. Comportarea la vibraţii

Vagonul de tramvai trebuie să funcţioneze în parametri nominali pe o cale de rulare care determină în circulaţie următoarele valori maxime ale vibraţiilor:

- 1 g pentru caroserie
- 3 g pentru rama boghiului
- 2 g pentru motorul de tracţiune
- 8 g pentru capul de osie

2.6 Condiţii pentru nivelul de zgomot admis

###### 2.6.1 Nivelul de zgomot maxim admis în exterior trebuie să se situeze la o valoare de 85 dB(A).

###### 2.6.2 Nivelul de zgomot maxim admis în interiorul salonului de pasageri trebuie să se situeze la o valoare de 80 dB(A).

###### 2.6.3 Nivelul de zgomot maxim admis în interiorul cabinei conducătorului de vehicul trebuie să se situeze la o valoare de 76 dBA, cu excepţia zgomotului produs de controler.

2.7 Rezistenţele de izolaţie

###### 2.7.1 Rezistenţele de izolaţie trebuie să fie mai mari de 10 MΩ în stare rece şi uscată, valori impuse în fişa de măsurători nr. 2.

###### 2.7.2 Rezistenţele de izolaţie trebuie să fie de 2 MΩ în stare umedă şi caldă. Proba de determinare a rezistenţei de izolaţie în stare umedă şi caldă este probă de investigaţie.

2.8 Valorile rezistenţelor electrice ale circuitelor de tracţiune şi auxiliare nu trebuie să se abată cu mai mult de ±20% faţă de valorile nominale înscrise în fişa de măsurători nr. 3.

2.9 Părţile conducătoare care nu sunt cale de curent sunt legate la masa vagonului prin legături de împământare. Rezistenţa electrică a unei legături de împământare este de cel mult 0,030 Ω în stare nouă.

2.10 Verificarea rigidităţii dielectrice conform CEI 77

La circuitele care lucrează la 750 Vcc, la aplicarea unei tensiuni de încercare de 3875 Vca 50Hz timp de 1 min., nu trebuie să apară străpungeri sau conturnări.

La circuitele care lucrează la 24 Vcc, la aplicarea unei tensiuni de încărcare de 750 Vca 50 Hz timp de 1 min., nu trebuie să apară străpungeri sau conturnări.

Punctele de aplicare sunt precizate în fişa de măsurători nr. 4

2.11 Toate circuitele ce lucrează la 750 Vcc au capătul minus legat la circuitul de retur. Rezistenţa electrică între firul de retur şi şină trebuie să fie mai mică de 0,1 Ω şi este trecută în Fişa de măsurători nr. 3.

2.12 Curentul de declanşare al întrerupătorului automat se reglează la 450 A ±5%.

2.13 La alimentarea pe întreaga plajă a tensiunii din reţea 750 Vcc(+20 % ; -30 %) cât şi la variaţia de la 0 la maxim a curentului absorbit de consumatori (toţi consumatorii de pe joasă cuplaţi) tensiunea în instalaţia de joasă tensiune trebuie să se încadreze între limitele 24 V ±20%.

2.14 Instalaţia de încărcare a bateriei trebuie să menţină starea ei de încărcare în timpul funcţionării la o tensiune maximă de 28,8 V.

2.15 Două baterii de acumulatori de tipul cu întreţinere redusă, în stare încărcată, trebuie să asigure consumul de energie în instalaţia de 24 Vcc timp de 30 min. cu excepţia consumatorilor clopot şi patină, ventilatoare încălzire şi nisipar.

2.16 Nivelul maxim al supratensiunilor de comutaţie este de 1200 V la 740 Vcc şi de 50 V la 24 Vcc.

2.17 Saltul curentului de tracţiune, la mersul normal al vagonului încărcat, în palier şi aliniament, cu cadenţa de manevrare a controlerului de două trepte/secundă, nu trebuie să depăşească 40 A cu excepţia primelor două trepte.

2.18 Saltul curentului de frânare, la mersul normal al vagonului încărcat, în palier şi aliniament, cu cadenţa de manevrare a controlerului de două trepte/secundă nu trebuie să depăşească 100 A, iar tensiunea nu va depăşi 1500 V (plecând de la vmax = 55 km/h).

2.19 Iluminatul normal este realizat în salonul de pasageri cu 26 tuburi fluorescente de 20 W alimentate prin intermediul unor invertoare electronice 24 Vcc/220 Vca.

2.20 Iluminatul de siguranţă în salonul de pasageri este realizat cu becuri incandescente de 5 W alimentate de la tensiunea de 24 V.

2.21 Condiţii privind semnalizările de funcţionare şi semnalizările de circulaţie

###### 2.21.1 Semnalizările de funcţionare la bordul vagonului trebuie să indice:

- întrerupătorul automat decuplat
- acţionarea frânelor de staţionare
- uşi deschise
- schimbarea direcţiei de mers
- faza lungă a farurilor
- avertizor sonor pentru acţionarea frânei de urgenţă, neacţionarea pedalei de autostop şi semnalului de alarmă: intensitatea 85 ÷ 90 dB(A)
- nefuncţionarea sursei statice
- avarii pompe hidraulice – instalaţie de frânare HK

###### 2.21.2 Semnalizările de circulaţie trebuie să indice:

- faruri fază lungă şi scurtă
- semnalizare intermitentă de direcţie, dreapta şi stânga
- semnalizare stop
- semnalizare mers înapoi
- semnalizare de poziţie
- semnalizare de ceaţă
- semnalizare sonoră de avertizare intensitate sonoră 85 ÷ 90 dB(A)

2.22 Condiţii privind parametrii dinamici

Vagoanele de tramvai neîncărcate trebuie să realizeze pe linie în palier şi aliniament viteza maximă de 55 km/h.

2.23 Condiţii privind geometria căii de rulare

###### 2.23.1 Vagoanele de tramvai trebuie să circule în curbe cu raza minimă de 18 m.

###### 2.23.2 Vagonul trebuie să poată parcurge o covată sau o cocoaşă în raza minimă de 800 m.

2.24 Demarajul vagonului gol, pe linie în palier şi aliniament trebuie să se realizeze cu o acceleraţie de maxim 1 m/s² .

2.25 Vagonul gol trebuie să frâneze de la viteza de 40 km/h până la staţionare astfel:

###### 2.25.1 La frânarea normală, respectiv frânare electrică reostatică şi frânare cu frâna cu resort, spaţiul de frânare trebuie să fie de maxim 42 m.

###### 2.25.2 La frânarea de urgenţă, respectiv frânarea electrică reostatică frânarea cu resort de acumulare şi frânarea cu patina la şină trebuie să fie de maxim 27 m.

2.26 Vagonul încărcat cu sarcină maximă, respectiv 200 kN trebuie să frâneze de la viteza de 40 km/h până la staţionare astfel:

###### 2.26.1 În frânare normală, respectiv frânare electrică reostatică şi frânare cu resort de acumulare, spaţiul de frânare trebuie să fie de maxim 50 m.

###### 2.26.2 La frânarea de urgenţă spaţiul de frânare trebuie să fie de maxim 30 m.

2.27 Vagonul de tramvai încărcat cu sarcină maximă trebuie să urce rampa de 60 ⁰/00 .

2.28 Vagonul de tramvai, încărcat cu sarcină maximă trebuie să fie imobilizat pe rampa de 60 ⁰/00 numai cu frâna de staţionare, timp de minim 10 minute.

2.29 Vagonul de tramvai, în stare goală trebuie să corespundă probelor privind siguranţa contra deraierii conform STR 680-89 MTTc.

2.30 Vagonul de tramvai circulând pe o linie conform “ Instrucţiuni tehnice departamentale pentru proiectarea şi construcţia liniilor de tramvai – PD 164 – 82”, va realiza un indice pentru calitatea de mers de maxim 3,25 pe platforma cabinei, lângă scaunul conducătorului.

2.31 Consumul specific de energie fără încălzire al vagonului cu încărcătură maximă trebuie să fie de 8 Wh/kNkm ±10%.

2.32 Deschiderea şi închiderea uşilor trebuie să se realizeze astfel:

- prin mişcare lină, fără blocări;
- prin realizarea cursei complete care să obţină lăţimea impusă deschiderii uşii de aprox. 1200 mm;
- prin închiderea completă încât să nu existe spaţiu între garniturile de cauciuc ale batantelor;
- închiderea şi deschiderea se realizează cu protecţia la obstacol.
- Funcţionarea uşilor este cuprinsă în „înstrucţiunile IFE nr. T407389 şi T407390”.

2.33 Vagoanele de tramvai sunt astfel concepute şi realizate încât în interiorul caroseriei şi în interiorul compartimentelor cu aparataj electric să nu poată pătrunde apa existentă din mediul ambiant (ploaie, zăpadă, viscol, ş.a.).

Se admit uşoare infiltraţii de apă:

- la balamalele geamurilor laterale rabatabile, condiţionat ca volumul de apă colectat de canalul geamului să poată fi evacuat prin gurile de scurgere prevăzute;
- la partea de jos a burdufului, condiţionat ca volumul de apă colectat să nu depăşească posibilitatea de evacuare prin gurile e scurgere. Se admite umectarea părţilor laterale ale burdufurilor datorită pătrunderii apei la cusături şi îmbinarea între burduf şi cadrul de prindere, fără a conduce la infiltraţii.
- în partea de jos a uşilor, la prima treaptă de urcare în vagon. Volumul de apă colectată să nu conducă la inundarea treptei.

2.34 Pantograful trebuie să îndeplinească următoarele condiţii:

###### 2.34.1 Pantograful trebuie să realizeze forţele de apăsare pe firul de contact conform diagramei din fişa de măsurători nr. 5.

###### 2.34.2 Forţa necesară retragerii pantografului de pe firul de contact în poziţia pliat, de către conducătorul vehiculului din cabină trebuie să aibă valoarea 15 ±3 daN.

2.35 Prin acţionarea semnalului de alarmă sau prin neacţionarea pedalei de siguranţă, vagonul trebuie frânat de către sistemele de frânare şi cu controlerul pe poziţia de MERS.

2.36 Acţionarea grătarului salvării trebuie să se producă în momentul când declanşatorul frontal întâlneşte pe cale un obstacol care dezvoltă asupra sa o forţă de 6 ±2 daN.

2.37 Supratemperaturile maxime admisibile după funcţionarea vagonului încărcat în timp de 8 ore la principalele agregate, subansamble şi compartimente trebuie să fie:

- reductor de tracţiune 60 °C
- lagăre cutie cap osie 55 °C
- motor tracţiune TN 71- colector 65 °C
- înfăşurare stator 115 °C
- înfăşurare indus 80 °C
- compartiment controler 50 °C
- elemente de conexiune 30 °C
- cabluri în jgheab 30 °C
- dulapuri de aparataj 25 °C

Vagonul va fi încărcat cu 80% din sarcina maximă.

2.38 Vitezometrul de bord trebuie să indice viteza vehiculului cu o precizie de 5%. Vitezometrul este dotat cu contor kilometraj .

2.39 Acoperiri de protecţie prin vopsire

Condiţii tehnice de calitate pentru protecţia prin vopsire sunt cele prevăzute în STAS 11568-83. Grosimea minimă a acoperirilor prin vopsire trebuie să fie de 90 µm. Cifra de aderenţă trebuie să fie de minim 2.

2.40 Acoperiri de protecţie prin zincare

Acoperirile de protecţie prin zincare la repere nefiletate se execută conform condiţiilor tehnice prevăzute în STAS 7222-90. Grosimea minimă a stratului de acoperire este de 12 µm pentru piesele din interiorul vagonului (condiţii grele de exploatare) şi de 25 µm pentru piesele din exteriorul vagonului (condiţii grele de exploatare).

Acoperirile de protecţie prin zincare la repere filetate se execută conform STAS 2700/8-82.

2.41 Acoperiri de protecţie prin oxidarea anodică a aliajelor de aluminiu

Acoperirile de acest tip se execută conform condiţiilor tehnice prevăzute în STAS 7043/1-93. Grosimea stratului de oxid trebuie să fie de 6÷15µm.

2.42 Condiţii privind fiabilitatea

Media previzională a timpului de bună funcţionalitate este de min. 20000 km pentru un nivel de încredere de 0,9. Media previzională a timpului de reparaţii anual este de 150 ore. Aceste indicatoare de fiabilitate permit utilizarea ciclului de revizii după cum urmează: - RT1 – revizia la 5000 km

- RT2 – revizia la 20000 km

2.43 Instalaţia electrică este protejată la scurtcircuit prin montarea unor aparate de protecţie speciale (întrerupătoare automate, siguranţe fuzibile). Supratensiunile accidentale pe instalaţia de alimentare de 750 V sunt eliminate cu descărcător DRVC montat pe acoperiş în apropierea pantografului. Bobinele aparatelor de comutaţie sunt prevăzute cu varistoare pentru tăierea vârfurilor de tensiune accidentală.

###### 2.43.1 Cablajele electrice sunt protejate prin montare în jgheaburi speciale iar trecerile între tronsoane prin manşoane şi aşezate astfel încât să realizeze frecări minime în timpul circulaţiei.

###### 2.43.2 Echipamentele electrice sunt montate în dulapuri sau compartimente speciale închise cu uşi dotate cu închizătoare la care are acces personalul specializat de întreţinere şi reparaţie.

###### 2.43.3 Vagonul de tramvai trebuie echipat cu 6 stingătoare de incendiu portabile cu praf şi CO2 .

2.44 Condiţii privind securitatea în exploatare

###### 2.44.1 Pentru înlăturarea comenzilor de mers şi frână involuntare, elementele de comandă sunt prevăzute cu indexări în poziţia de lucru sau repaus.

###### 2.44.2 Elementele de comandă sunt amplasate astfel încât să permită manevrarea comodă din poziţia şezând pe scaun a conducătorului vehiculului.

###### 2.44.3 Fiecare comandă este inscripţionată definind clar rolul ei.

2.45 Vagonul este prevăzut cu ştergătoare de parbriz cu acţionare electrică la

Un = 24 Vcc. In fiecare cabină se montează instalaţia de spălare parbriz.

2.46 Fiecare post de conducere este prevăzut cu aerotermă cu degivrator, iar salonul de pasageri este dotat cu 12 rezistenţe de încălzire montate în pereţii laterali ai vagonului, iar temperatura din interiorul salonului de călători este supravegheată prin intermediul unui termostat general reglat din fabrică şi sigilat.

2.47 Degivratoarele din cabine pot functiona si numai ca ventilatoare.

2.48 Verificarea bilanţului energetic pentru instalaţia de 24 Vcc

Instalaţia de încărcare a bateriilor de acumulatori va asigura regimul normal de încărcare al acestora, iar bilanţul energetic raportat la bateria de acumulatori este pozitiv.

2.49 Circuitele de alimentare cu tensiunea de 24 Vcc pentru sistemul de frână cu patină electromagnetică la şină trebuie să asigure alimentarea timp de maxim 15 minute fără apariţia unor defecte în circuitele electrice respective.

2.50 Vagonul de tramvai încărcat 80%, în circulaţie timp de 30 minute cu un singur motor de tracţiune, trebuie să funcţioneze fără defecţiuni cu respectarea parametrilor de la pct. 2.37. Proba se execută pentru ambele motoare.

2.51 La acţionarea comenzilor nisiparelor, acestea trebuie să funcţioneze permiţând curgerea nisipului pe şină şi la comanda de întrerupere trebuie să oprească curgerea nisipului pe şină. Nisiparele sunt dotate cu rezistenţe de încălzire pentru menţinerea uscată a nisipului.

2.52 Condiţia de planeitate

Pentru intervalul dimensiunilor nominale între 1000÷2000 mm (raportat la latura mai lungă a suprafeţei) abaterea la planeitate va fi maxim 2 mm.

2.53 Verificarea funcţionării dispozitivelor de defrânare manuală a actuatoarelor hidraulice H&K.

3. REGULI PENTRU VERIFICAREA CALITĂŢII

3.1 Produsele care fac obiectul prezentului standard se supun următoarelor încercări şi verificări:

- de tip
- de lot
- de investigare

###### 3.1.1 Încercările şi verificările de tip se execută de constructor şi au ca scop verificarea condiţiilor tehnice.

###### 3.1.1.1 Încercările şi verificările de tip se execută:

a) asupra prototipului
b) la introducerea modificărilor constructive sau a procesului tehnologic care influenţează asupra funcţionării sau calităţii vagonului
c) periodic la 4 ani
d) în cazul reluării fabricaţiei (după fiecare întrerupere) asupra capului de serie

###### 3.1.1.2 Încercările şi verificările indicate în cap. 3.1.1.1 a); c); d) se efectuează în totalitate. În cazul în care produsul nu satisface toate condiţiile, el se va remedia şi se va prezenta la o nouă încercare plecându-se de la încercarea care nu a reuşit.

###### 3.1.1.3 Încercările şi verificările de la cap. 3.1.1.1 b), pot fi parţiale, cuprinzând numai verificarea condiţiilor tehnice care sunt influenţate de modificarea introdusă.

###### 3.1.1.4 Numărul vagoanelor de tramvai care se supun încercărilor de tip este de 1 buc.

###### 3.1.2 Încercările şi verificările de lot se execută de către constructor şi au ca scop garantarea că produsul de serie este echivalent cu produsul omologat. Se execută asupra tuturor vagoanelor fabricate.

3.1.3 Încercările şi verificările de investigare sunt încercări speciale, cu caracter facultativ, care sunt efectuate pe un singur produs, în scopul de a da informaţii suplimentare asupra performanţelor sale; efectuarea lor nu este impusă decât dacă a fost expres specificată în contractul dintre părţi. Rezultatele încercărilor de investigare nu sunt opozabile acceptării materialului (CEI-77; CEI-1133:1997).

3.2 Lista verificărilor şi încercărilor de tip şi de lot

Nr.crt. | Denumirea încercării sau verificării | Condiţia tehnică | Metode de încercare | Felul încercării
1. | Verificare respectării documentaţiei şi tehnologiilor de execuţie şi a certificatelor de conformitate şi calitate pentru materiale, ansamble şi subansamble componente ale vagoanelor V3A-93 | 2.1. | 4.1. | T, L
2. | Măsurarea dimensiunilor de gabarit | 2.2 | 4.2 | T, L
3. | Măsurarea sarcinii vagonului | 2.3. | 4.3. | T, L
4. | Verificarea calităţii suspensiei Determinări statice | 2.4. | 4.4. | T, L
5. | Verificarea comportării la vibraţii | 2.5. | 4.5. | I
6. | Măsurarea nivelului de zgomot | 2.6. | 4.6. | T, L
7.1 | Măsurarea rezistenţei de izolaţie In stare rece | 2.7. | 4.7. | T, L
7.2 | Măsurarea rezistenţei de izolaţie In stare caldă şi umedă | 2.7 | 4.7 | I
8. | Măsurarea valorilor rezistenţelor electrice ale circuitelor de tracţiune şi auxiliare | 2.8. | 4.8. | T, L
9. | Verificarea legăturilor la masa vagonului | 2.9. | 4.9. | T, L
10. | Verificarea rigidităţii dielectrice a instalaţiei de 750 V | 2.10. | 4.10. | T, L
11. | Verificarea circuitelor de retur la instalaţia de 750 V | 2.11. | 4.11. | T, L
12. | Verificarea funcţionării întrerupătorului automat, reglaje şi la scurtcircuit | 2.12. | 4.12. | T, L
13. | Verificarea menţinerii constante a tensiunii în instalaţia electrică în circuitele auxiliare | 2.13. | 4.13. | T, L
14. | Verificarea funcţionării instalaţiei de încărcare a bateriei | 2.14. | 4.14. | T, L
15. | Verificarea autonomiei asigurată de bateriile de acumulatori | 2.15 | 4.15 | T
16. | Măsurarea nivelului maxim al supratensiunilor de comutaţie | 2.16. | 4.16. | I
17. | Măsurarea curenţilor de demaraj pentru vagon încărcat în palier şi aliniament | 2.17. | 4.17. | T
18. | Măsurarea curenţilor de frânare pentru vagon încărcat în palier şi aliniament | 2.18. | 4.18. | T
19. | Verificarea funcţionării iluminatului normal al salonului de pasageri | 2.19. | 4.19. | T, L
20. | Verificarea iluminatului de siguranţă al salonului de pasageri | 2.20. | 4.20. | T, L
21. | Verificarea funcţionării semnalizărilor optice şi acustice ale vagonului | 2.21. | 4.21. | T, L
22. | Măsurarea vitezei maxime în palier şi aliniament | 2.22. | 4.22. | T
23. | Verificarea înscrierii în curbă cu raza de 18 m şi a mersului în covată şi cocoaşă | 2.23. | 4.23. | T, L
24. | Măsurarea acceleraţiei maxime la pornire cu vagonul gol, în palier şi aliniament | 2.24. | 4.24. | T
25. | Măsurarea spaţiului de frânare sau acceleraţia cu vagon gol prin frânare normală şi frânare de urgenţă | 2.25. | 4.25. | T, L
26. | Măsurarea spaţiului de frânare sau acceleraţia cu vagon încărcat prin frânare normală şi frânare de urgenţă | 2.26. | 4.26. | T
27. | Verificarea posibilităţii de urcare pentru rampa de 60 ⁰/00 a vagonului încărcat | 2.27. | 4.27. | T
28. | Verificarea imobilizării pe rampa de 60 ⁰/00 a vagonului încărcat, cu frâna de staţionare | 2.28. | 4.28. | T
29. | Verificarea funcţionării vagonului gol la probele privind siguranţa contra deraierii | 2.29. | 4.29. | I
30. | Verificarea indicelui calităţii de mers | 2.30. | 4.30. | I
31. | Măsurarea consumului specific de energie la vagon încărcat | 2.31. | 4.31. | T
32. | Verificarea funcţionării uşilor | 2.32. | 4.32. | T, L
33. | Verificarea etanşeităţii la apă a caroseriei | 2.33. | 4.33. | T, L
34. | Verificarea caracteristicilor de funcţionare ale pantografului: determinarea diagramei forţă / deplasare | 2.34. | 4.34. | T, L
35. | Verificarea funcţionării semnalelor de alarmă şi instalaţiei de siguranţă | 2.35. | 4.35. | T, L
36. | Verificarea funcţionării mecanismului de salvare | 2.36. | 4.36. | T, L
37. | Măsurarea supratemperaturii la principalele agregate, subansamble şi compartimente după o funcţionare de 8 ore cu vagon încărcat (80% din sarcina maximă) | 2.37. | 4.37. | T
38. | Verificarea funcţionării vitezometrului de bord | 2.38. | 4.38. | T
39. | Verificarea acoperirilor de protecţie prin vopsire | 2.39. | 4.39. | T
40. | Verificarea acoperirilor de protecţie prin zincare | 2.40. | 4.40. | T
41. | Verificarea acoperirilor de protecţie prin oxidare anodică a aliajelor de Al | 2.41. | 4.41. | T
42. | Verificarea condiţiilor privind fiabilitatea | 2.42. | 4.42. | T
43. | Verificarea condiţiilor privind protecţia contra focului | 2.43. | 4.43. | T, L
44. | Verificarea condiţiilor privind securitatea în exploatare | 2.44. | 4.44. | T, L
45. | Verificarea funcţionării ştergătorului de şi a instalaţiei de spălare parbriz | 2.45. | 4.45. | T, L
46. | Verificarea funcţionării instalaţiei de încălzire şi ventilaţie | 2.46. | 4.46. | T, L
47 | Verificare degivratoare ca ventilatoare | 2.47 | 4.47 | T,L
48. | Verificarea bilanţului energetic de joasă tensiune (24 V) | 2.48. | 4.48. | T
49. | Verificarea frânei cu patină cu alimentare la 24 V | 2.49. | 4.49. | T, L
50. | Verificarea funcţionării cu un singur motor pentru vagon încărcat | 2.50. | 4.50. | I
51. | Verificarea funcţionării nisiparelor | 2.51. | 4.51. | T, L
52. | Planeitate | 2.52 | 4.52 | T, L
53. | Verificarea funcţionării dispozitivelor de defrânare manuală a actuatoarelor hidraulice H&K | 2.53 | 4.53 | T,L

Notă: Pentru toate probele indicate în tabel, cu excepţia celor de investigaţie şi a celor ce se execută în exteriorul RATB, se vor completa documente corespunzătoare pentru certificare în scris a execuţiei probelor respective. Indicele de numerotare corespunde cu numărul probelor din prezentul standard

4. METODE DE ÎNCERCARE ŞI VERIFICARE

4.1 Condiţiile tehnice de la pct. 2.1 se verifică astfel:

4.1.1 Calitatea materialelor şi subansamblelor achiziţionate din comerţ se verifică pe baza declaraţiei de conformitate şi garanţie emisă de producător. În caz de dubiu, constructorul va verifica caracteristicile respective la furnizor sau cu mijloace proprii în conformitate cu prevederile standardului de produs.

###### La constatarea unei abateri de la calitatea materialului sau tipul componentelor, se va verifica existenţa derogării acordate de proiectantul produsului, în caz contrar acesta se va respinge.

###### 4.1.2 Verificarea dimensiunilor şi abaterilor de formă şi poziţie se face prin măsurarea acestora şi compararea cu cele din documentaţia de execuţie şi cu valorile înscrise în fişele de măsurători.

###### 4.1.3 Verificarea aspectului şi execuţiei se face vizual prin examinarea suprafeţelor pieselor componente şi a cordoanelor de sudură. Pentru verificarea cordoanelor de sudură se foloseşte şi lupa de atelier x 8.

###### 4.1.4 Toate SDV-urile şi AMC-urile folosite vor fi verificate periodic (1 an pentru AMC-uri).

4.2 Condiţiile tehnice de la pct. 2.2 se verifică astfel:

- vagonul este aşezat pe palier şi aliniament cu pantograful pliat. Cu ajutorul unor echere şi rigle se proiectează pe sol dimensiunile ce se măsoară în plan orizontal.
- în mod similar se procedează în plan vertical
- dimensiunile se măsoară cu ruleta şi se înscriu în fişa de măsurători.

4.3 Condiţiile tehnice de la pct. 2.3 se verifică astfel:

Vagonul gol este aşezat pe standul de verificare a sarcinii pe roată care măsoară sarcinile suportate pentru fiecare roată. Datele se înscriu în Fişa de măsurători de la anexa 6I.

4.4 Condiţiile tehnice de la pct. 2.4 se verifică astfel:

4.4.1 Vagonul în stare încărcată, se plasează pe o linie în palier şi aliniament dotată cu canal de lucru.

4.4.2 Cotele se măsoară folosind o riglă plană pentru materializarea suprafeţei şinei şi una gradată pentru măsurarea cotei între bază şi şină.

4.4.3 Vagonul în stare neîncărcată, se plasează pe o linie în palier şi aliniament dotată cu canal de lucru.

4.4.4 Cotele se măsoară folosind o riglă plană pentru materializarea suprafeţei şinei şi una gradată pentru măsurarea cotei între bază şi şină.

4.5 Condiţiile tehnice de la pct. 2.5 se verifică astfel:

Se măsoară acceleraţia de vibraţii globală, cel puţin în următoarele puncte:

- un cap de osie atacantă parte cuplă reductor a boghiului motor I;
- rama boghiului motor I deasupra capului de osie menţionat anterior;
- grupul motor reductor al boghiului motor I (2 puncte unul pe reductor şi unul pe motor);
- cutiile cu echipament la nivelul podelei pe tronsoanele A şi B (compartimente aparataj);
- plafonul tronsonului A (în zona pantografului);
- tabloul de bord şi scaun manipulant.

Măsurătorile se efectuează cu vagon încărcat.

Aceasta este probă de investigaţie.

4.6 Nivelul de zgomot de la pct. 2.6 se măsoară astfel:

###### 4.6.1 Nivelul de zgomot în exterior se măsoară la distanţa de 7,5 m faţă de axul căii de rulare, la înălţimea de 1,5 m, vagonul având viteza de 40 km/h. Măsurarea se face pe linie cu trafic redus şi fără curbe.

###### 4.6.2 Nivelul de zgomot în interiorul salonului de pasageri cu ferestrele închise se măsoară la înălţimea de 1,5 m faţă de nivelul podelei în următoarele zone:

- boghiu motor I
- boghiuri purtătoare – articulaţii
- boghiu motor II

###### Vagonul va circula cu viteza de 40 km/h cu sursa statică în funcţiune, pe linie cu trafic redus fără curbe.

###### 4.6.3 Nivelul de zgomot în interiorul cabinei conducătorului de vehicul se măsoară în cabină la înălţimea de 1,2 m cu uşa cabinei şi ferestrele închise, vagonul circulând cu viteza de 40 km/h pe linie cu trafic redus, fără curbe şi fără a avea aeroterma pornită.

4.7 Rezistenţele de izolaţie pct. 2.7 se verifică separat pentru instalaţia de 750 Vcc şi separat pentru instalaţia de 24 Vcc.

Verificările se fac de către personal specializat, care va avea grijă ca, prin ştrafări şi deconectări, să nu producă, în timpul verificării, defecţiuni ale echipamentelor, acordându-se atenţie deosebită echipamentelor electronice.

Valorile măsurate se scriu în fişa de măsurători nr. 2.

Măsurarea rezistenţei de izolaţie în stare caldă şi umedă este probă de investigaţie.

4.8 Valorile rezistenţelor electrice ale circuitelor de tracţiune şi auxiliare se determină astfel:

4.8.1 Măsurarea rezistenţelor electrice ale circuitelor de tracţiune.

- Mers înainte şi frână

4.8.2 Măsurarea rezistenţelor electrice ale circuitelor auxiliare:

- Circuite încălzire

Verificările se fac de către personal specializat, care va avea grijă ca, prin ştrafări şi deconectări, să nu producă, în timpul verificării, defecţiuni ale echipamentelor, acordându-se atenţie deosebită echipamentelor electronice.

Valorile măsurate se scriu în fişa de măsurători nr. 3.

4.9 Verificarea legăturilor de împământare, pct. 2.9, se face de către personal specializat, care va avea grijă ca, prin ştrafări şi deconectări, să nu producă, în timpul verificării, defecţiuni ale echipamentelor, acordându-se atenţie deosebită echipamentelor electronice.

4.10 Verificarea rigidităţii dielectrice, pct. 2.10, se face de către personal specializat, care va avea grijă ca, prin ştrafări şi deconectări, să nu producă, în timpul verificării, defecţiuni ale echipamentelor, acordându-se atenţie deosebită echipamentelor electronice.

Verificarea se executa intre nodurile indicate în fişa de măsurători nr.4.

4.11 Condiţia tehnică pct. 2.11 se verifică de către personal specializat, care va avea grijă ca, prin ştrafări şi deconectări, să nu producă, în timpul verificării, defecţiuni ale echipamentelor, acordându-se atenţie deosebită echipamentelor electronice. Se completează fişa de măsurători nr.3.

4.12 Funcţionarea întrerupătorului automat, pct. 2.12, se verifică de către personal specializat, care va avea grijă ca, prin ştrafări şi deconectări, să nu producă, în timpul verificării, defecţiuni ale echipamentelor, acordându-se atenţie deosebită echipamentelor electronice.

4.13 Pentru verificările de la pct. 2.13 se cuplează sursa statică. Se cuplează şi se decuplează toţi consumatorii instalaţiei de 24 Vcc. Probele se efectuează pentru tensiunea max. şi min. a reţelei de alimentare. Rezultatul este satisfăcător dacă variaţia tensiunii secundare în aceste condiţii se încadrează între limitele

24±20% V.

4.14 Funcţionarea instalaţiei de încărcare a bateriei, pct. 2.14, se verifică astfel:

Se pune în funcţiune sursa statică urmărind regimul de încărcare, respectiv stabilizarea după 10 minute a valorii curentului de max. 20 A. După funcţionarea timp de trei ore a sursei fără consumatori tensiunea va fi maxim 28,8 Vcc.

După funcţionarea timp de 8 ore, valoarea curentului trebuie să fie maxim 10 A iar tensiunea de maxim 28,8 Vcc.

4.15 Condiţia tehnica, pct. 2.15, se verifica astfel: După executarea operaţiunilor pct. 4.14 se opreşte funcţionarea sursei statice si se circula cu vagonul timp de 30 min.

După deconectarea tuturor consumatorilor de joasă tensiune, valoarea măsurată, cu ajutorul unui voltmetru cu clasa de precizie 1,5 , va fi de cel puţin 18 Vcc.

4.16 Verificările de la pct. 2.16, se efectuează de către personal specializat, care va avea grijă ca, prin ştrafări şi deconectări, să nu producă, în timpul verificării, defecţiuni ale echipamentelor, acordându-se atenţie deosebită echipamentelor electronice.

Aceasta este probă de investigaţie

4.17 Măsurarea curentului în tracţiune, pct. 2.17. se efectuează de către personal specializat, care va avea grijă ca, prin ştrafări şi deconectări, să nu producă, în timpul verificării, defecţiuni ale echipamentelor, acordându-se atenţie deosebită echipamentelor electronice.

4.18 Măsurarea curentului de frânare pct. 2.18 se efectuează de către personal specializat, care va avea grijă ca, prin ştrafări şi deconectări, să nu producă, în timpul verificării, defecţiuni ale echipamentelor, acordându-se atenţie deosebită echipamentelor electronice.

4.19 Condiţia tehnică de la pct. 2.19. se verifică astfel:

Proba se execută cu vagonul oprit, cu pantograful pe firul de contact. La cuplarea întrerupătorului specializat pentru iluminat, acestea trebuie să se aprindă.

4.20 Condiţia tehnică de la pct. 2.20 se verifică astfel:

Proba se execută cu vagonul oprit, cu pantograful pe firul de contact. Cu iluminatul normal în funcţiune se retrage pantograful de pe firul de contact. După 25 secunde trebuie să se aprindă iluminatul incandescent de siguranţă cu alimentare de la 24 Vcc.

4.21 Condiţia tehnica de la pct. 2.21. se verifică astfel:

Probele se execută cu vagonul oprit, cu pantograful pe firul de contact. Se cuplează alimentarea pe joasa tensiune din comutatorul de pe panoul cu monopolari. Se urmăreşte atingerea curentului de încărcare a bateriei şi tensiunea de 28,8 V pe voltmetru.

4.21.1 Verificarea semnalizărilor de funcţionare la nivelul vagonului:

- se decuplează disjunctorul automat şi se verifică dacă lampa de pe panoul de bord semnalizează decuplarea

- se acţionează frâna de staţionare şi se verifică dacă lămpile de pe panoul de bord semnalizează frânarea;

- se acţionează pe rând toate butoanele de deschidere a uşii; trebuie să se aprindă lămpile de semnalizare pentru uşi deschise. La acţionarea butoanelor pentru închidere, lămpile de semnalizare trebuie să se stingă;

- se acţionează comutatorul de direcţie de la bordul vagonului, in direcţiile stânga şi dreapta, verificându-se aprinderea lămpii de semnalizare direcţie la bord;

- se acţionează comutatorul luminii farurilor pe faza lunga şi se verifică apariţia semnalului lămpii de bord;

- se acţionează un semnal de alarmă si se urmăreşte apariţia semnalului acustic de avertizare

- se acţionează frâna cu patină la şina şi se urmăreşte apariţia semnalului acustic de avertizare ;

- se porneşte sursa statică şi se urmăreşte stingerea lămpii de semnalizare a încărcării bateriei.

- se acţionează maneta inversor pe poziţia mers înapoi şi se va verifica dacă se aprind lămpile de semnalizare mers înapoi.

4.21.2 Verificarea semnalizărilor de circulaţie:

- se acţionează comutatorul de fază a farurilor de la 0 Ia faza scurtă şi la faza lungă urmărindu-se lumina farurilor;

- se acţionează comutatorul schimbării de direcţie, pe rând stânga şi dreapta, urmărind funcţionarea intermitenta a lămpii faţă, laterale şi spate;

- se acţionează controlerul pe mers frâna, se acţionează frâna cu patină la şină verificând aprinderea lămpilor de stop spate;

- se acţionează maneta axului inversor pe poziţia mers înapoi şi se verifică aprinderea luminilor albe in lampa combinată spate;

- se acţionează butonul pentru funcţionarea semnalului acustic, intensitatea trebuie să fie 85÷90 dB(A) măsurată la 7 m pe calea de rulare la înălţimea de 1,5 m;

- se acţionează controlerul de poziţie de mers si nu se acţionează pedala de siguranţă a circulaţiei şi autostop urmărind declanşarea semnalului acustic de avertizare.

4.22 Viteza maxima a vagonului pct. 2.22. se stabileşte cu vagonul gol, pe o, linie în palier şi aliniament. Demarajul se execută manevrând normal controlerul şi menţinându-l pe ultima treapta de mers până la stabilizarea vitezei maxime, urmărind-o pe vitezometrul de bord.

4.23 Înscrierea în curbe de 18 m, pe covată şi pe cocoaşă cu raza minimă de 800 m a vagonului, pct. 2.23, se verifică astfel :

- prin mişcarea sa în curbă pe o distanţă de 3÷5 m;

- prin mişcarea sa pe covată şi cocoaşă:

- boghiurile motoare şi purtătoare nu trebuie să atingă nici o parte a caroseriei;

- nu trebuie să existe frecări ale cablurilor instalaţiei electrice în zona articulaţiei;

- măştile exterioare din zona articulaţiei nu trebuie să atingă elementele caroseriei, respectiv scheletul şi îmbrăcămintea exterioară;

- în interiorul salonului de pasageri, platforma articulaţiei şi balustradei nu trebuie să atingă elemente ale caroseriei;

- se verifică integritatea burdufurilor înainte şi după probă.

4.24 Condiţia tehnică pct. 2.24 se stabileşte astfel :

- Vagonul gol, circulă pe o linie în palier şi aliniament;

- Demarajul vagonului se realizează prin trecere progresivă a controlerului pe fiecare treaptă de mers până în momentul când se constată scăderea valorii acceleraţiei;

- Măsurătorile se execută cu aparat tip Frenotest sau alt tip de aparat corespunzător.

4.25 Măsurătorile de frânare pentru vagon gol, pct. 2.25., se execută astfel :

- Vagonul circulă pe o linie în palier şi aliniament pe timp liniştit, cu şina curăţată şi uscată;

- măsurătorile se execută de 3 ori făcând media aritmetica a acestora;

- Începerea frânării se execută în dreptul unui reper vizat in momentul când viteza este stabilizată la 40 km/h;

- Se cronometrează timpul de frânare şi se măsoară spaţiul de frânare de la reperul la care a început frânarea până la locul de oprire al vagonului.

4.25.1 Spaţiul de frânare pentru frânarea normala, pct. 2.25.1, se determina prin acţionarea controlerului pe treptele de frânare reostatică până la viteza de cca. 10 km/h, de la această viteză se acţionează frâna cu resort până la oprirea vehiculului.

4.25.2 Spaţiul de frânare pentru frânare urgenţă, pct. 2.25.2, se determină prin acţionarea controlerului pe treptele de frânare reostatică şi simultan prin acţionarea comutatorului frânelor cu patină la şină, de la viteza de cca. 10 km/h se acţionează şi frâna cu resort de acumulare până la oprire.

4.26 Măsurătorile de frânare pentru vagon cu sarcina maximă, pct. 2.26, se execută în acelaşi mod cu cel definit pentru vagon gol.

4.27 Încercarea de urcare a vagonului cu sarcină max. pe rampa de 60⁰/00, pct. 2.27, se execută astfel:

- vagonul circulă pe rampa de 60⁰/00;

- se frânează, opreşte şi demarează, operaţia repetându-se de 3 ori în aceste condiţii, la demaraj nu se admite:

- deconectarea disjunctorului;

- deplasarea înapoi.

4.28 Încercarea de imobilizarea a vagonului cu sarcina maximă pe rampa de 60⁰/00, pct. 2.28, se executa astfel :

- vagonul circula normal pe rampa de 60⁰/00;

- se frânează normal şi se acţionează frâna de staţionare, operaţia repetându-se de trei ori.

In aceste condiţii vagonul, trebuie sa staţioneze frânat numai cu frâna de staţionare timp de 10 min.

4.29 Încercările privind siguranţa contra deraierii, pct. 2.29 se execută cu vagonul gol conform STR 680-88 emis de MT. Se execută proba de verificare a rigidităţii torsionale pe o linie in palier si aliniament dotată cu cupoane de şină echipate cu mărci tensometrice.

Aceasta este probă de investigaţie.

4.30 Determinarea calităţii de mers, pct. 2.30., se efectuează cu vagonul gol, pe o linie normală de circulaţie valorile Wz trebuie sa fie inferioare lui 3,25 la viteza de 40 km/h. Metodologia de verificare este conforma cu STR 680-88 emisa de M.T. pentru vehicule motoare.

Aceasta este probă de investigaţie.

4.31 Determinarea consumului specific de energie, pct. 2.31, este necesar a se executa stabilind condiţii cât mai apropiate de cele reale de trafic, datorita faptului că depinde de factori ce variază foarte mult ca: modul de conducere al manipulantului, gradul de ocupare în timp a căii de rulare, starea căii de rulare diferita pe fiecare traseu, variaţia tensiunii de alimentare, etc.

In aceste condiţii, beneficiarul stabileşte un traseu de circulaţie reprezentativ ştiind că o ora de trafic cu aglomeraţie medie, prin măsurare rezultând un consum mediu.

Proba se efectuează cu respectarea următoarelor condiţii :

4.31.1 Vagonul circula cu încărcătura maxima.

4.31.2 Demarajul vagonului se face in mod progresiv prin acţionarea treptată a treptelor controlerului.

4.31.3 In atingerea vitezei maxime legale de 50 km/h controlerul se pune pe 0, vagonul circulând lansat.

4.31.4. Trecerea pe frâna se face funcţie de frânare până la staţie şi acţionând de la circa 10 km/h frâna cu resort de acumulare.

4.31.5. Instalaţia de măsurare se montează în aşa fel încât să poată înregistra toţi consumatorii.

4.31.6 Proba se repetă de trei ori, efectuând media valorilor măsurate. Instalaţia de măsurare a consumului energetic se va monta în aşa fel încât contorul să fie deconectat la regimul de frânare reostatică prin întreruperea alimentării contorului – curent şi tensiune sau numai curent.

Aceasta este probă de investigaţie.

4.32 Verificarea funcţionării uşilor, pct. 2.32, se realizează astfel

- vagonul staţionează în staţie cu refugiu şi este alimentat la reţeaua 750 Vcc pentru ca sursa statică să încarce bateriile;

- se acţionează de 3 ori închiderea şi deschiderea tuturor uşilor, urmărindu-se dacă funcţionarea se realizează fără blocări, cu o mişcare continuă;

- se va urmări deschiderea uşilor la o lăţime de aprox. 1200 mm;

- se verifică dacă uşile de închid complet, fără a rămâne spaţiu între garniturile de etanşare ale batantelor;

- se verifică imposibilitatea deplasării vagonului cu uşile deschise.

4.33 Verificarea etanşării vagonului, pct. 2.33, în timpul probei, se realizează astfel:

- vagonul se introduce într-o instalaţie pentru verificarea etanşeităţii la ploaie, în timpul probei fiind scos din reţeaua de alimentare;

- uşile, ferestrele, capacele de ventilaţie şi capacele echipamentelor sunt închise;

- ploaia artificială se menţine timp de 5 min. conform STAS 9470-73.

- Viteza de cădere a picăturii de apă de până la 7,5 m/s şi un debit de 7,5 l/min m² conform STAS 11218-83

Proba se consideră satisfăcătoare dacă nu există scurgeri de apă în interiorul vagonului şi cutiilor de aparate.

Se admit uşoare infiltraţii de apă:

- la balamalele geamurilor laterale rabatabile, condiţionat ca volumul de apă colectat de canalul geamului să poată fi evacuat prin gurile de scurgere prevăzute;

- la partea de jos a burdufului, condiţionat ca volumul de apă colectat să nu depăşească posibilitatea de evacuare prin gurile e scurgere;

- în partea de jos a uşilor, la prima treaptă de urcare în vagon. Volumul de apă colectată să nu conducă la inundarea treptei. Se admite umectarea părţilor laterale ale burdufurilor datorită pătrunderii apei la cusături şi îmbinarea între burduf şi cadrul de prindere, fără a conduce la infiltraţii.

4.34 Verificarea funcţionării pantografului, pct. 2.34, se realizează astfel:

4.34.1. Măsurarea distanţelor pe verticală se obţine cu o riglă gradată amplasată pe postamentul pantografului, iar forţele se măsoară cu un dinamometru fixat de centrul traversei superioare.

Măsurarea forţelor se face atât la ridicarea pantografului din poziţia pliat cât şi la coborârea până la poziţia pliat la următoarele cote: 750 mm, 1750 mm, 2400 mm.

Valorile obţinute se marchează pe diagrama din Fişa de măsurători nr. 5.

Funcţionarea se consideră satisfăcătoare dacă valorile obţinute se încadrează în limitele diagramei.

4.34.2. Măsurarea forţelor de retragere a pantografului.

Măsurarea forţelor se face atât la ridicarea pantografului din poziţia pliat cât şi la coborârea până la poziţia pliat la următoarele cote : 750 mm, 1750 mm, 2400 mm.

Valorile obţinute se marchează pe diagrama din fişa de măsurători.

Funcţionarea se considera satisfăcătoare dacă valorile obţinute se încadrează în limitele diagramei.

4.34.3. Măsurarea forţei de retragere a pantografului de pe firul de contact de către manipulant, se execută prin utilizarea unui dinamometru. Această forţa trebuie să se încadreze in valoarea 15±3 daN.

4.35 Verificarea funcţionării semnalului de alarmă, pct. 2.35, se realizează astfel:

- vagonul circulă cu viteza de 30...40 km/h;

- în momentul acţionării semnalului de alarmă trebuie să intre în funcţiune sistemul de frânare, oprind vagonul.

4.36 Verificarea funcţionării mecanismului de salvare:

- vagonul staţionează pe linie, frânat cu frâna de staţionare;

- de declanşatorul frontal al grătarului salvării se trage cu dinamometrul până la acţionarea şi căderea la nivelul şinei a acestuia;

- se consideră funcţionarea corectă dacă forţa de declanşare este de 6 ±2 daN;

- se normează şi se verifică menţinerea contra declanşării accidentale.

4.37 Verificarea supratemperaturilor maxime admisibile la principalele agregate, subansamble şi compartimente, pct. 2.37, se execută după funcţionarea vagonului în condiţii de trafic timp de min. 8 ore. Proba se poate realiza după parcursul în care se măsoară consumul specific de energie.

4.37.1 La următoarele agregate şi compartimente se măsoară temperatura prin introducerea unui termometru tehnic cu bimetal (sau alt aparat de măsură a temperaturii având o clasă de precizie de 5%) în carcasele sau incinta respectiva:

Reductoarele de tracţiune, compartimentul controlerului, dulapurile de aparataj şi jgheaburile de cabluri. Temperaturile măsurate nu trebuie să depăşească valorile indicate la pct. 2.37.

4.37.2 La următoarele agregate se măsoară temperatura prin lipirea de ele a unui termometru de contact : motor tracţiune TN71 şi lagăre cutie cap osie.

4.38 Verificarea vitezometrului de bord, pct. 2.38 se face la furnizorul echipamentului, pe un stand de probe corespunzător şi se verifică prin sondaj valorile indicate pe aparatul de verificare faţă de un aparat etalon.

4.38.1 Viteza vagonului care circulă pe o linie în palier şi aliniament se verifică prin cronometrarea parcurgerii unei distanţe măsurate, vagonul circulând cu o viteză stabilizată.

4.39 Verificarea acoperirilor de protecţie prin vopsire se execută pe următoarele eşantioane .

- 10 epruvete din tabla vopsita în condiţii identice cu vagonul, la dimensiunile 15x15x150 mm;

Eşantioanele vopsite se verifică pentru condiţii foarte grele de exploatare. Se execută următoarele verificări astfel:

- aspect vizual;

- aderenţa conform SRISO 2409-1994;

- grosimea conform SRISO 2808-1993;

- comportarea în mediu de căldură umedă conform STAS 8393/4-81, STAS 8393/5-81;

- verificarea rezistenţei la coroziune în mediu de ceaţă salină conform STAS 8393/6-82.

Nu se admit defecte sau abateri de la valorile nominale.

4.40 Verificarea acoperirilor de protecţie prin zincare se executa pe următoarele eşantioane :

- rezistori demaraj pentru condiţii de exploatare foarte grele cu utilizare în exterior;

- cutie cu rezistenţe adiţionale pentru condiţii de exploatare grele cu utilizare în interior.

Se execută următoarele verificări astfel:

- aspect vizual, STAS 7222-90;

- aderenţa, STAS 7222-90;

- comportarea în mediu de căldura umedă, STAS 8393/8-87;

- verificarea rezistenţei la coroziune în mediu de ceaţă salină cf. STAS 8393/6-82;

- grosime cf. STAS 6854-90 pentru repere nefiletate;

- grosime cf. STAS 2700/8-90 pentru repere filetate.

Nu se admit defecte sau abateri de la valorile nominale.

4.41 Verificarea acoperirilor de protecţie prin oxidarea anodică a aliajelor de Al se execută cf. STAS 7043/1-93.

Probele se execută pe două rame de fereastră.

Se execută următoarele verificări astfel:

- aspect vizual;

- grosime cf. STAS 7043/2-90;

- Comportare în mediul de căldura umeda cf. STAS 8393/5-81;

- verificarea rezistenţei la coroziune în mediu de ceaţa salină cf. STAS 8393/6-82.

Nu se admit defecte sau abateri de la valori nominale.

4.42 Verificarea condiţiilor de fiabilitate, pct. 2.42, se execută în modul următor:

Se urmăreşte în exploatare timp de 1 an un lot de 10 vagoane. Culegerea datelor şi interpretarea statică a indicatorilor de fiabilitate şi a mediei timpului de reparaţie se face in exploatare pe baza unui raport tip de exploatare (anexa 6).

Defectele care se vor lua in consideraţie nu se referă la piese de schimb şi echipament de uzură indicat în Instrucţiunile de întreţinere şi exploatare.

In raportul de exploatare se vor nota defectele şi cauzele defectelor specificându-se dacă sunt:

- inerente ansamblului defectat;

- datorate unei defectări din cauza utilizării necorespunzătoare;

- datorită acţiunii unor cauze externe ansamblului defectat;

- datorate uzurii normale;

- necunoscute.

Valorile spaţiului parcurs se notează intre două defectări sau două tipuri de intervenţii planificate.

Timpul de lucru activ se refera numai la timpii necesari pentru constatare, intervenţie şi probe. încercări, nu se cuprind timpii de imobilizare, timpii de aşteptare pentru reparaţie. Nivelul de intervenţie trebuie să specifice consumul de manoperă, materiale şi piese. Media timpului de funcţionare se calculează cu relaţia:

mf = t’ j (km) unde:

p = numărul defectelor timp de un an;

t'j = spaţiul parcurs între defectări.
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

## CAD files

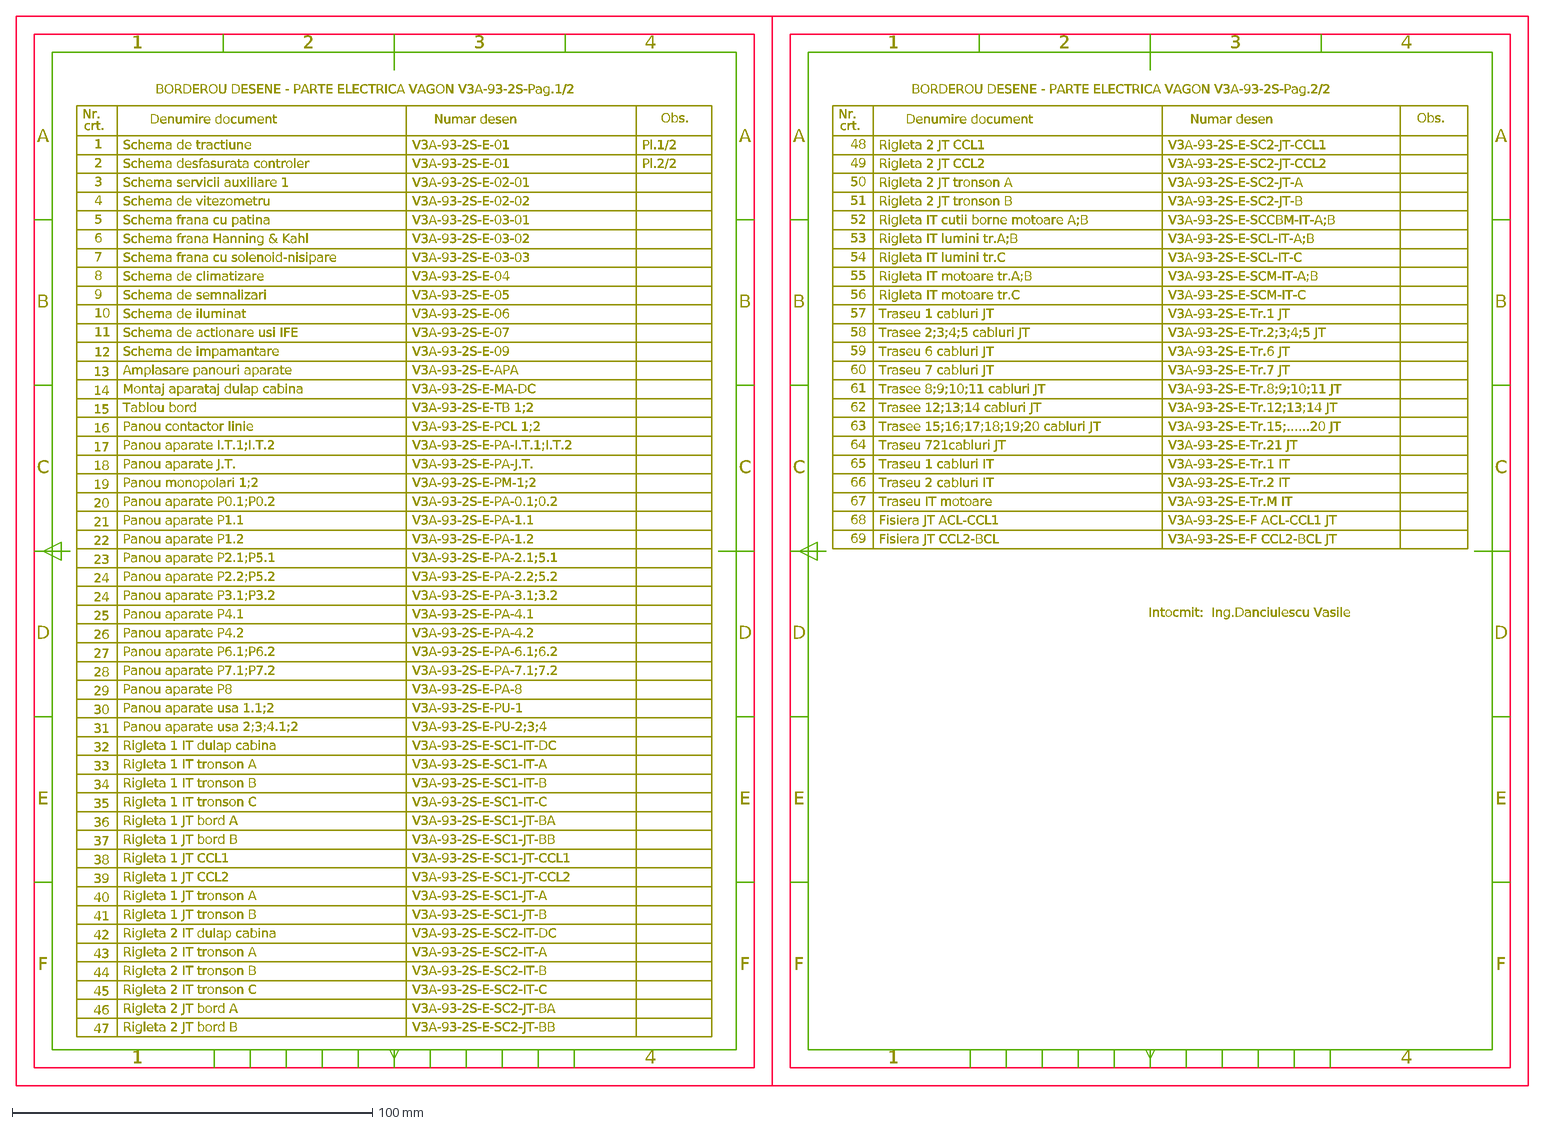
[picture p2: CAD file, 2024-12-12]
BORDEROU DESENE.dxf
F
E
D
C
B
A
4
3
2
1
BORDEROU DESENE - PARTE ELECTRICA VAGON V3A-93-2S-Pag.1/2
Nr.
crt.
Denumire document
Numar desen
Obs.
Schema de tractiune
V3A-93-2S-E-01
Pl.1/2
Schema desfasurata controler
Pl.2/2
Schema servicii auxiliare 1
V3A-93-2S-E-02-01
V3A-93-2S-E-02-02
Schema de vitezometru
Schema frana cu patina
V3A-93-2S-E-03-01
5
6
Schema frana Hanning & Kahl
V3A-93-2S-E-03-02
Schema frana cu solenoid-nisipare
7
V3A-93-2S-E-03-03
8
Schema de climatizare
V3A-93-2S-E-04
9
Schema de semnalizari
V3A-93-2S-E-05
10
Schema de iluminat
V3A-93-2S-E-06
11
Schema de actionare usi IFE
V3A-93-2S-E-07
Schema de impamantare
12
V3A-93-2S-E-09
13
Amplasare panouri aparate
V3A-93-2S-E-APA
14
Montaj aparataj dulap cabina
V3A-93-2S-E-MA-DC
15
Tablou bord
V3A-93-2S-E-TB 1;2
16
Panou contactor linie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

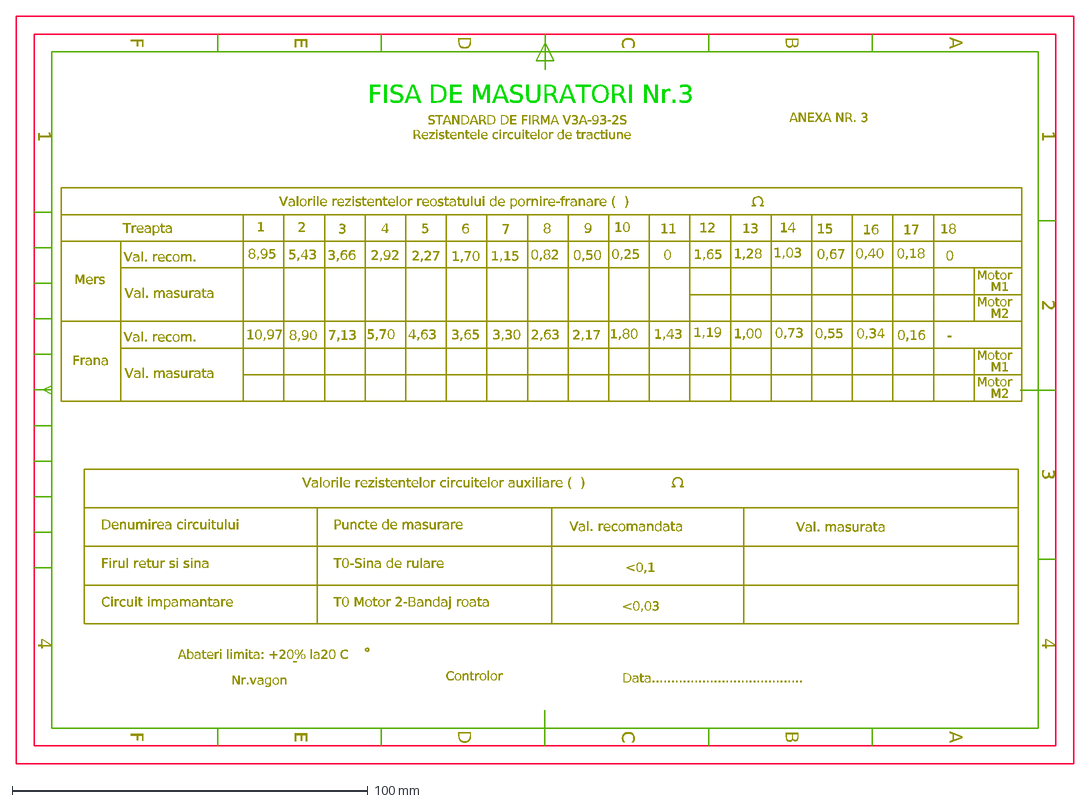
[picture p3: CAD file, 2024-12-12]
FISE DE MASURATORI/FISA DE MASURATORI 3.dxf
F
E
D
C
B
A
4
3
2
1
FISA DE MASURATORI Nr.3
STANDARD DE FIRMA V3A-93-2S
Rezistentele circuitelor de tractiune
Nr.vagon
Controlor
Data.......................................
ANEXA NR. 3
8,95
10,97
Mers
Frana
Treapta
17
0,18
0,16
0,67
1,28
1,65
0,25
0,50
1,15
1,70
0,82
2,92
5,43
3,66
2,27
2,17
4,63
5,70
8,90
7,13
3,30
3,65
2,63
1,00
1,19
1,80
1,43
0,55
0,34
0,73
Valorile rezistentelor reostatului de pornire-franare ( )
8
7
6
5
13
12
0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

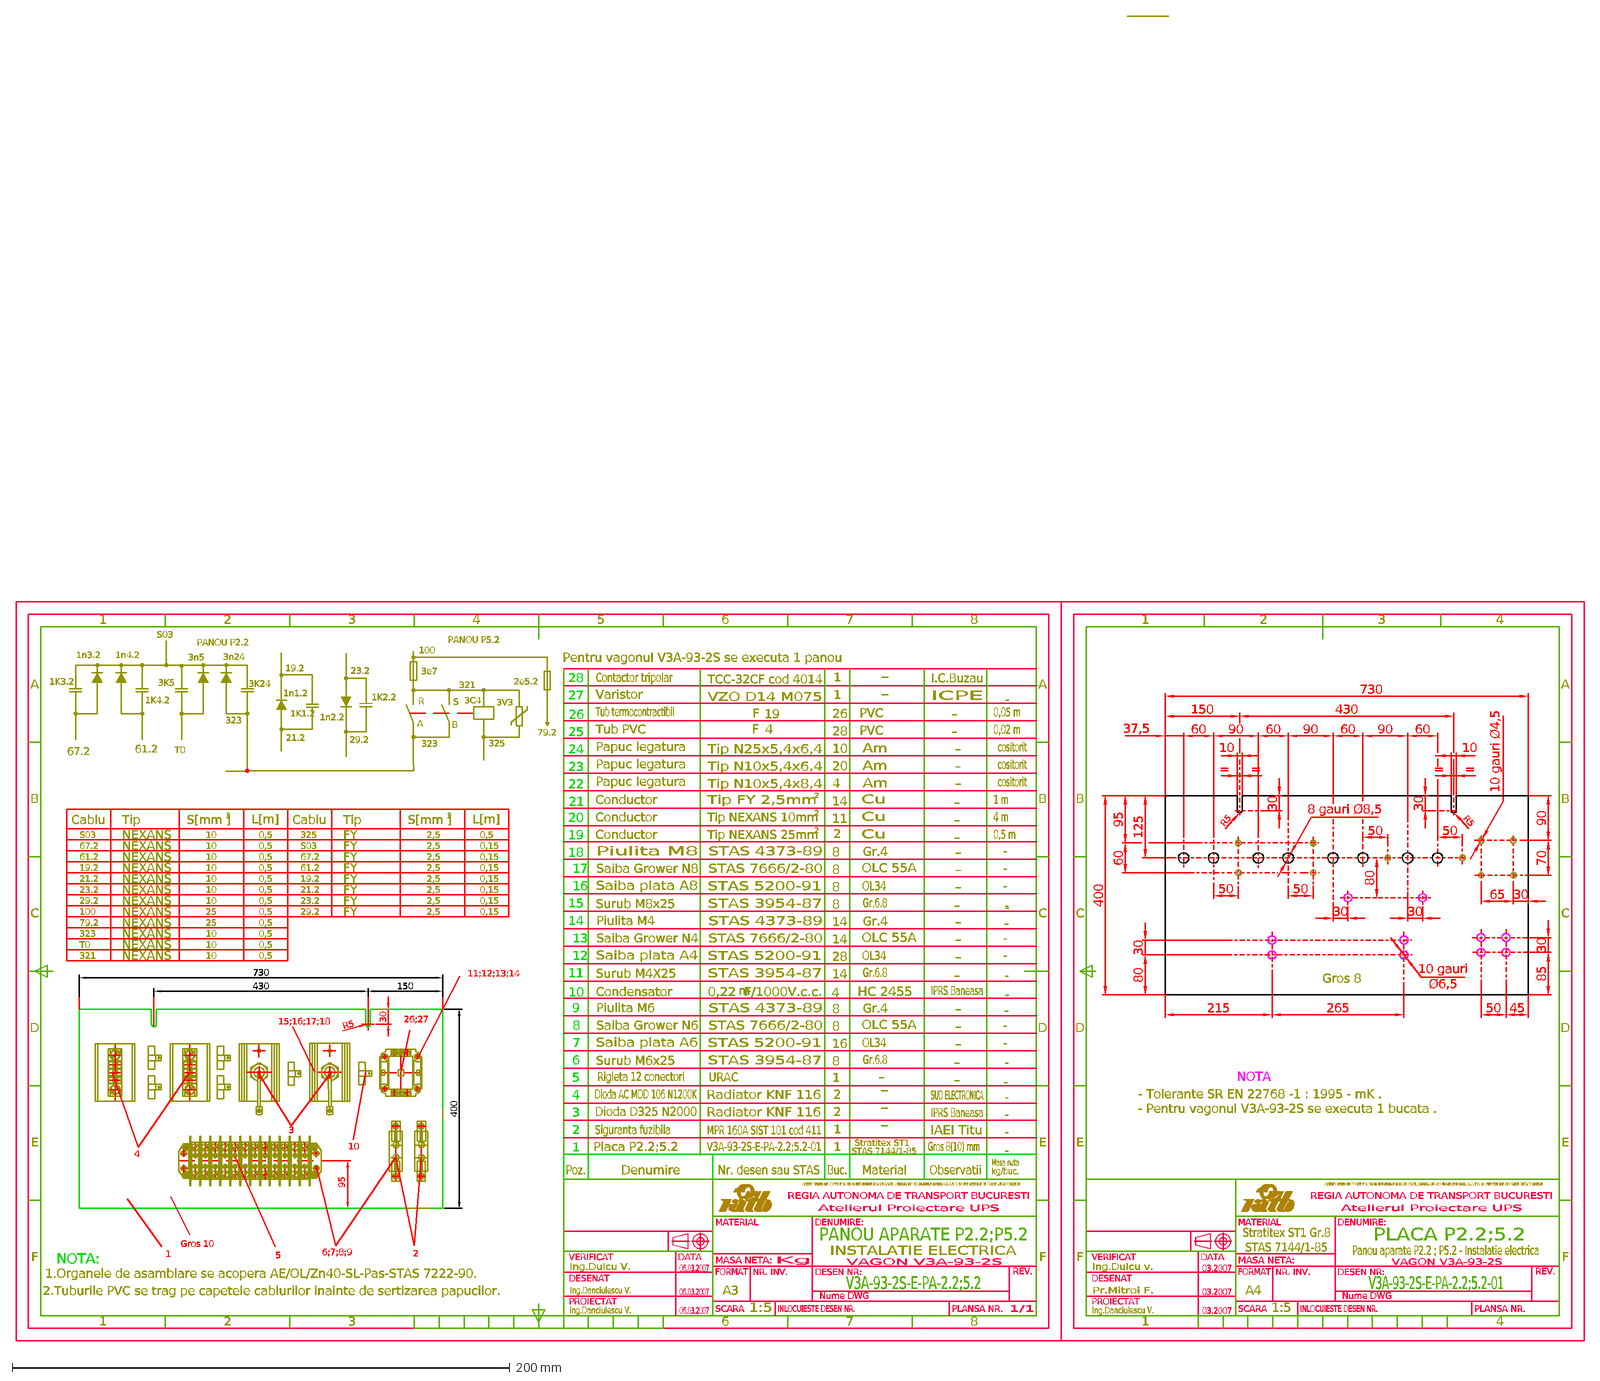
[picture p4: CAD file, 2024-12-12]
PANOURI APARATE/PANOU P2.2; P5.2.dxf
8
7
6
5
4
3
1
2
F
E
D
C
B
A
PANOU APARATE P2.2;P5.2
INSTALATIE ELECTRICA
VAGON V3A-93-2S
V3A-93-2S-E-PA-2.2;5.2
Nume DWG
1/1
A3
1:5
Kg
Ing.Duicu V.
06.03.2007
Ing.Danciulescu V.
ACEST DESEN SE POATE FOLOSI IN INTREGIME SAU PE PARTI, ASIGURAND CA NUMELE SI SIGLA R.A.T.B. SA FIE VIZIBILE PE ORICE REPRODUCERE.
PLANSA NR.
REV.
DESEN NR:
INLOCUIESTE DESEN NR.
NR. INV.
SCARA
MASA NETA:
FORMAT
DENUMIRE:
REGIA AUTONOMA DE TRANSPORT BUCURESTI
MATERIAL
PROIECTAT
DESENAT
DATA
VERIFICAT
Atelierul Proiectare UPS
Poz.
Denumire
Nr. desen sau STAS
Buc.
Observatii
Material
Masa neta
kg/buc.
323
325
3V3
3e7
PANOU P5.2
2e5.2
79.2
R
S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

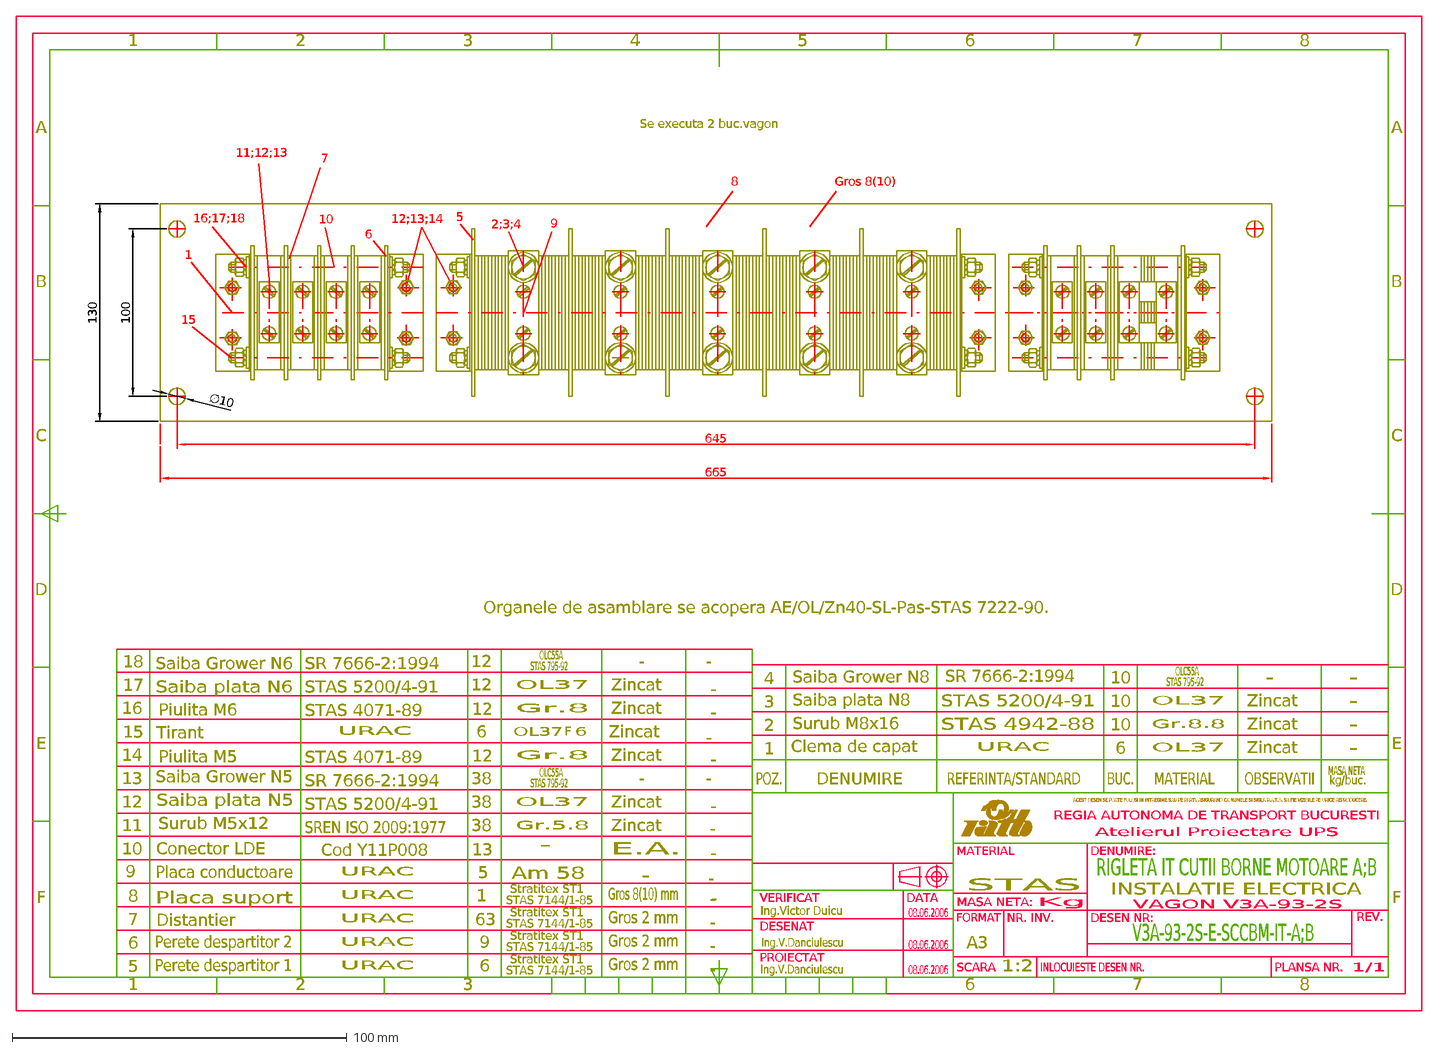
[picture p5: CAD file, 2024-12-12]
SIRURI DE CLEME/RIGLETA IT CUTII BORNE MOTOARE TRONSOANE A;B.dxf
E.A.
8
7
6
5
4
3
1
2
F
E
D
C
B
A
Se executa 2 buc.vagon
Placa conductoare
Conector LDE
9
10
63
13
Am 58
-
Surub M5x12
14
Tirant
11
12
15
38
12;13;14
16;17;18
11;12;13
2;3;4
BUC.
RIGLETA IT CUTII BORNE MOTOARE A;B
INSTALATIE ELECTRICA
VAGON V3A-93-2S
V3A-93-2S-E-SCCBM-IT-A;B
1/1
A3
1:2
STAS
Kg
Ing.Victor Duicu
08.06.2006
Ing.V.Danciulescu
ACEST DESEN SE POATE FOLOSI IN INTREGIME SAU PE PARTI, ASIGURAND CA NUMELE SI SIGLA R.A.T.B. SA FIE VIZIBILE PE ORICE REPRODUCERE.
PLANSA NR.
REV.
DESEN NR:
INLOCUIESTE DESEN NR.
NR. INV.
SCARA
MASA NETA:
FORMAT
DENUMIRE:
REGIA AUTONOMA DE TRANSPORT BUCURESTI
MATERIAL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

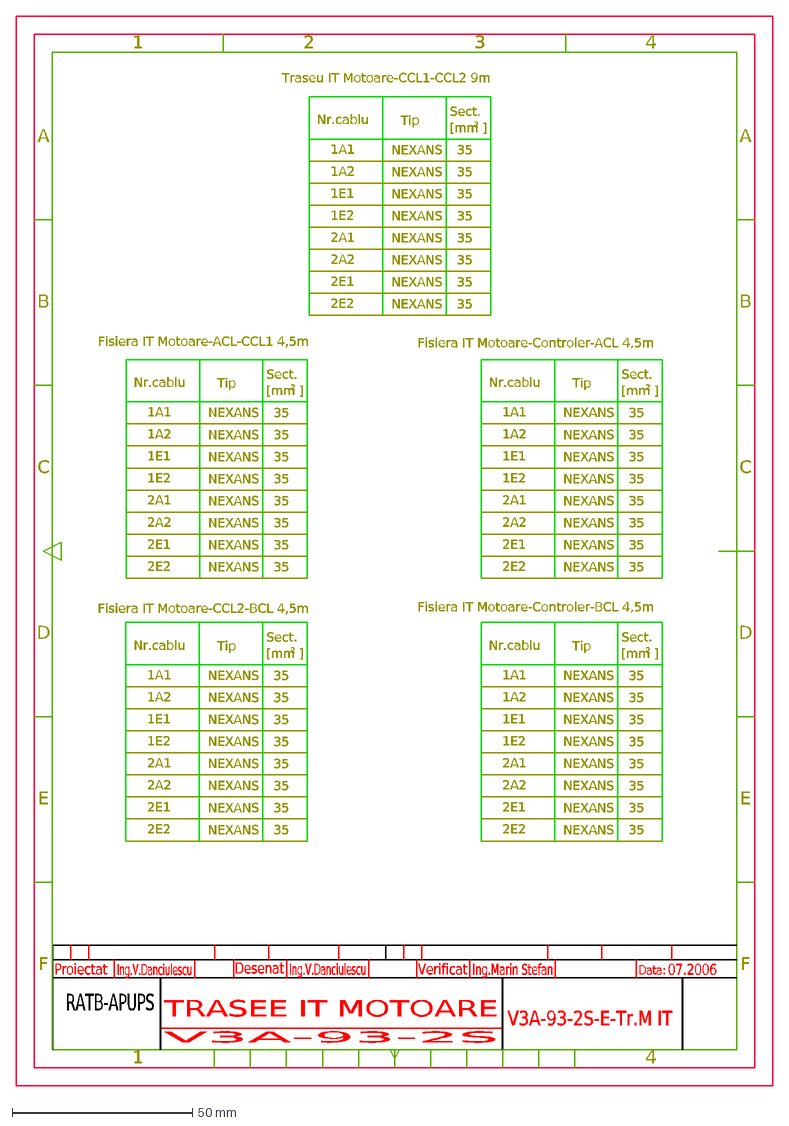
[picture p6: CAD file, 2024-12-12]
TRASEE SI JURNALE DE CABLURI/TRASEE IT MOTOARE.dxf
TRASEE IT MOTOARE
V3A-93-2S
V3A-93-2S-E-Tr.M IT
Ing.V.Danciulescu
Ing.Marin Stefan
07.2006
RATB-APUPS
Proiectat
Verificat
Desenat
Data:
F
E
D
C
B
A
1
4
2E1
2E2
2A1
2A2
2
Traseu IT Motoare-CCL1-CCL2 9m
NEXANS
1A1
1E1
1E2
1A2
Nr.cablu
Tip
35
Sect.
[mm ]
3
Fisiera IT Motoare-ACL-CCL1 4,5m
Fisiera IT Motoare-CCL2-BCL 4,5m
Fisiera IT Motoare-Controler-BCL 4,5m
Fisiera IT Motoare-Controler-ACL 4,5m

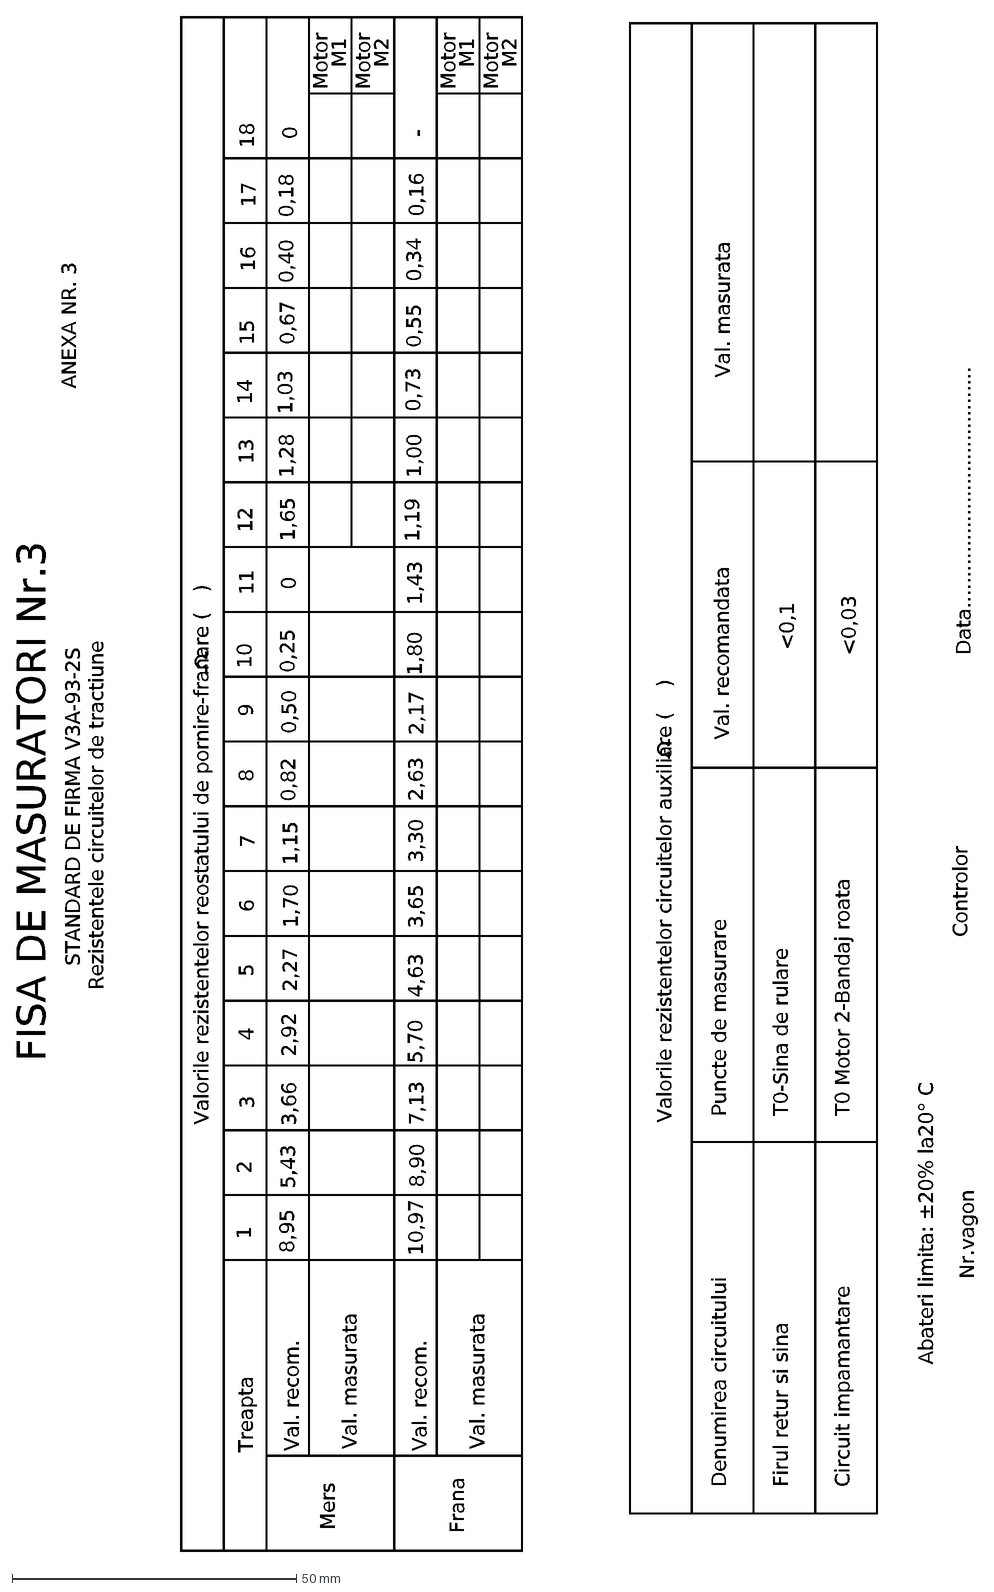
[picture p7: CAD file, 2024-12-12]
FISE DE MASURATORI/FISA DE MASURATORI 3 - ARIAL.dxf
FISA DE MASURATORI Nr.3
STANDARD DE FIRMA V3A-93-2S
Rezistentele circuitelor de tractiune
Nr.vagon
Controlor
Data.......................................
ANEXA NR. 3
8,95
10,97
Mers
Frana
1
Treapta
17
0,18
0,16
0,67
1,28
1,65
0,25
0,50
1,15
1,70
0,82
2,92
5,43
3,66
2,27
2,17
4,63
5,70
8,90
7,13
3,30
3,65
2,63
1,00
1,19
1,80
1,43
0,55
0,34
0,73
4
3
2
8
7
6
5
13
12
0
10
9
11
16
15
0,40
14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

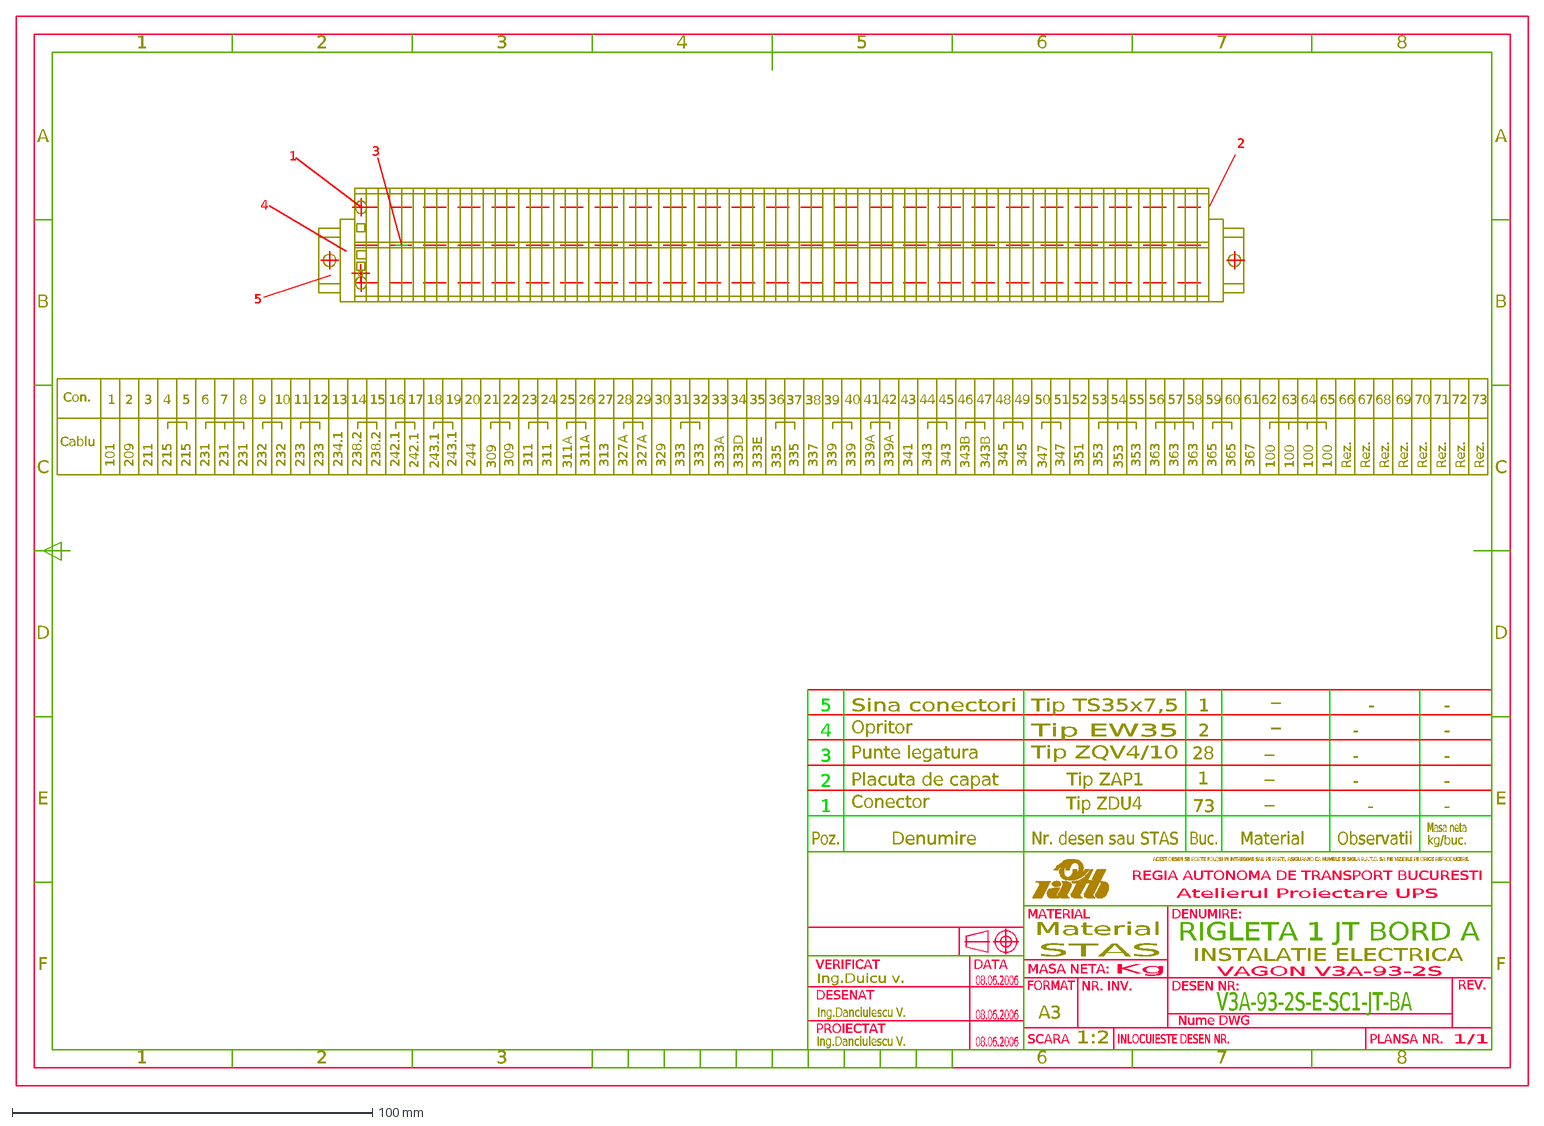
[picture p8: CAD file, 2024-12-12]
SIRURI DE CLEME/RIGLETA 1 JT BORD A.dxf
Observatii
RIGLETA 1 JT BORD A
INSTALATIE ELECTRICA
VAGON V3A-93-2S
V3A-93-2S-E-SC1-JT-BA
Nume DWG
1/1
A3
1:2
Material
STAS
Kg
Ing.Duicu v.
08.06.2006
Ing.Danciulescu V.
ACEST DESEN SE POATE FOLOSI IN INTREGIME SAU PE PARTI, ASIGURAND CA NUMELE SI SIGLA R.A.T.B. SA FIE VIZIBILE PE ORICE REPRODUCERE.
PLANSA NR.
REV.
DESEN NR:
INLOCUIESTE DESEN NR.
NR. INV.
SCARA
MASA NETA:
FORMAT
DENUMIRE:
REGIA AUTONOMA DE TRANSPORT BUCURESTI
MATERIAL
PROIECTAT
DESENAT
DATA
VERIFICAT
Atelierul Proiectare UPS
Denumire
Poz.
Nr. desen sau STAS
Buc.
kg/buc.
Masa neta
Tip ZQV4/10
Punte legatura
1
Conector
2
3
Tip ZDU4
73
28
-
Sina conectori
5
4
Tip EW35
Tip TS35x7,5
Placuta de capat
Tip ZAP1
8
7
6
F
E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

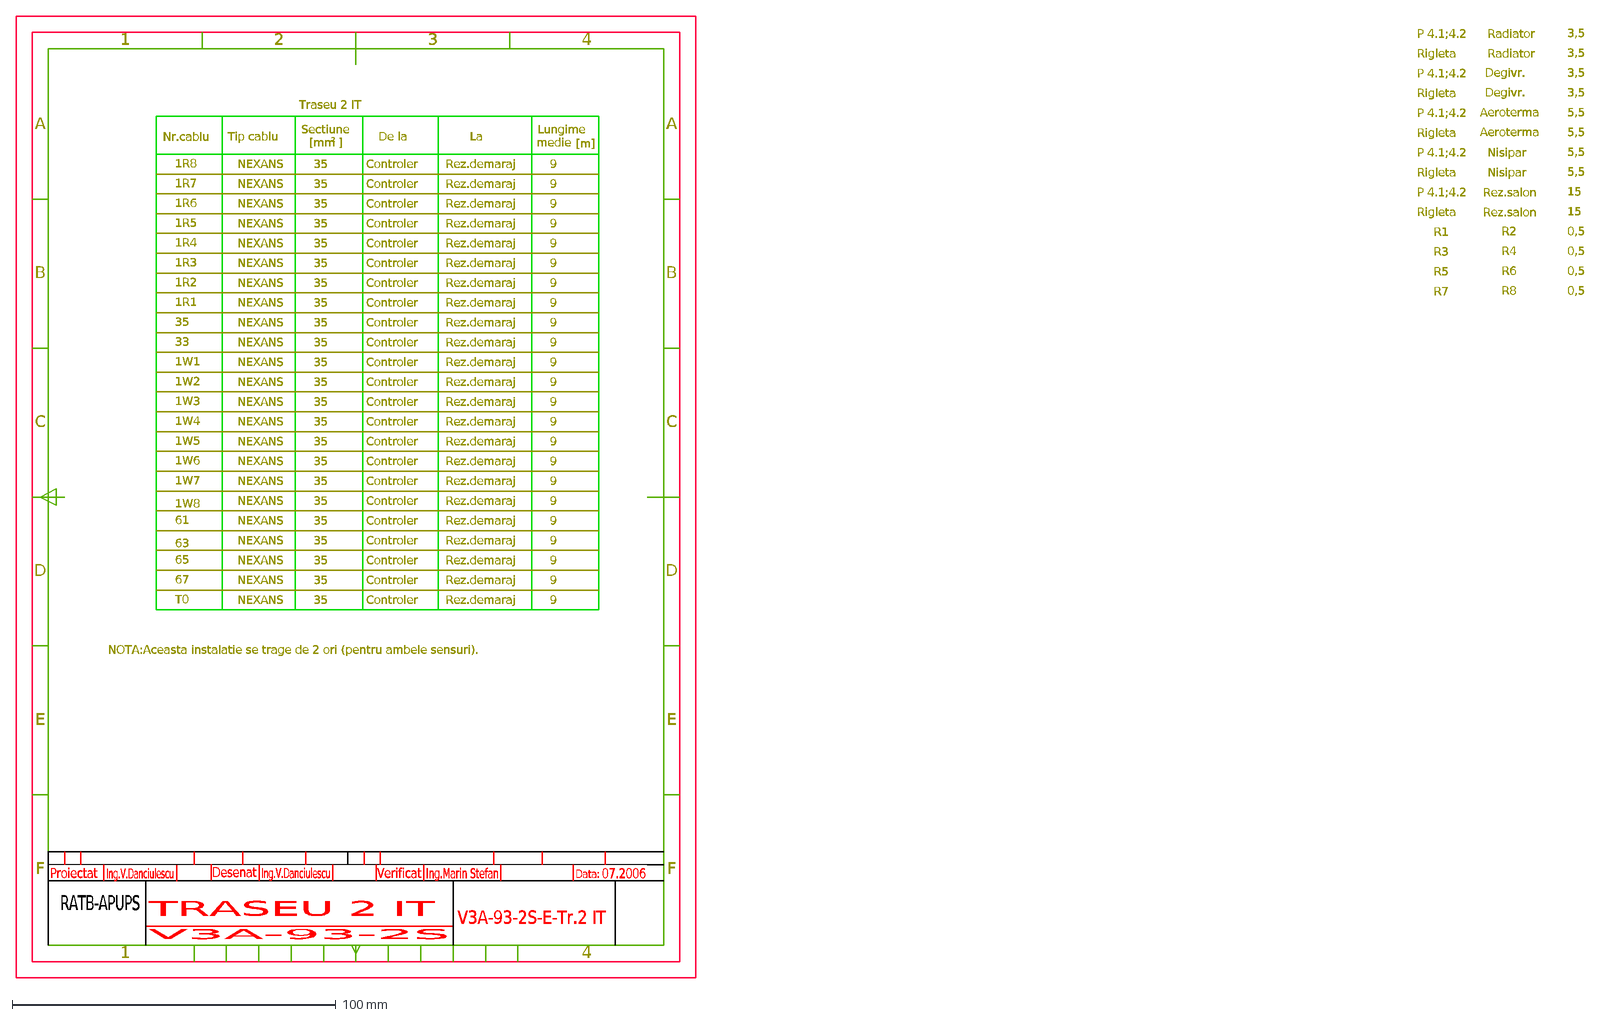
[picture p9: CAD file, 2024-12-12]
TRASEE SI JURNALE DE CABLURI/TRASEU 2 IT.dxf
F
E
D
C
B
A
4
3
2
1
1W8
TRASEU 2 IT
V3A-93-2S
V3A-93-2S-E-Tr.2 IT
Ing.V.Danciulescu
Ing.Marin Stefan
07.2006
RATB-APUPS
Proiectat
Verificat
Desenat
Data:
NEXANS
67
T0
63
65
61
Rez.demaraj
La
1R6
1W7
1W6
1W5
1W4
1W3
1W2
1W1
33
35
1R1
1R2
1R3
1R4
1R5
Tip cablu
Nr.cablu
1R8
1R7
Traseu 2 IT
Sectiune
[mm ]
De la
Controler
Lungime
[m]
P 4.1;4.2
Rigleta
R1
R3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

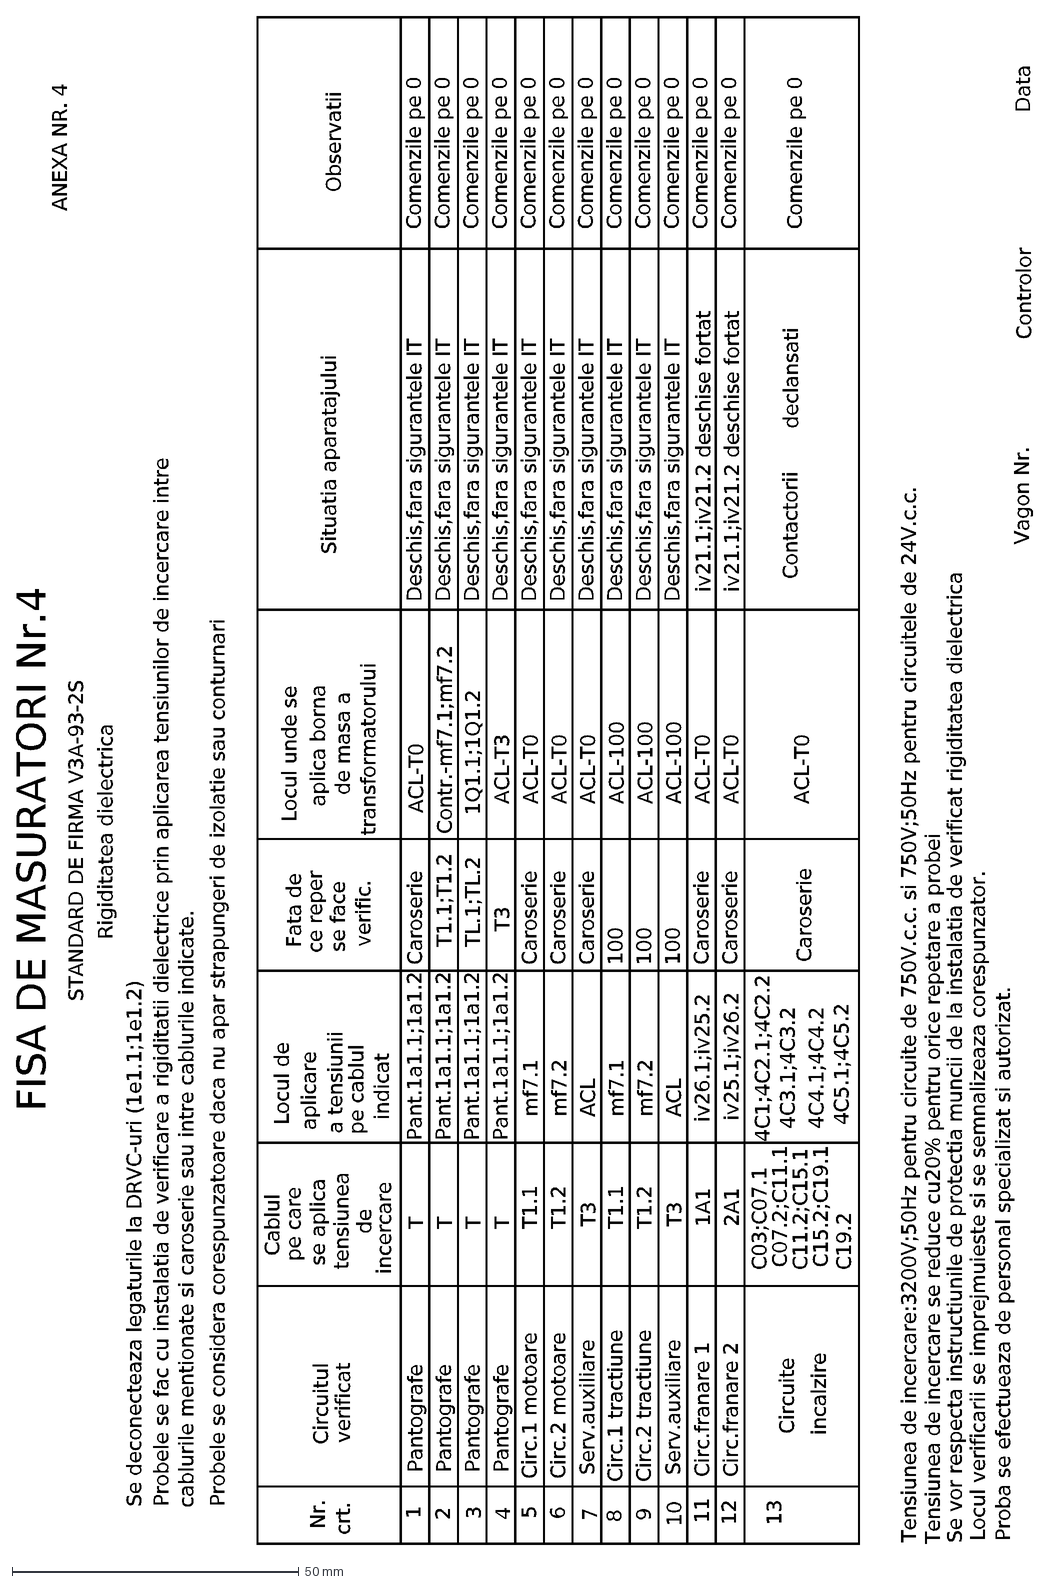
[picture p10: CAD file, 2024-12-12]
FISE DE MASURATORI/FISA DE MASURATORI 4 - ARIAL.dxf
FISA DE MASURATORI Nr.4
STANDARD DE FIRMA V3A-93-2S
Rigiditatea dielectrica
Probele se fac cu instalatia de verificare a rigiditatii dielectrice prin aplicarea tensiunilor de incercare intre
cablurile mentionate si caroserie sau intre cablurile indicate.
Nr.
crt.
Circuitul
verificat
Cablul
pe care
se aplica
tensiunea
de
incercare
Fata de
ce reper
se face
verific.
Locul de
aplicare
a tensiunii
pe cablul
indicat
Locul unde se
aplica borna
de masa a
Situatia aparatajului
Observatii
Tensiunea de incercare:3200V;50Hz pentru circuite de 750V.c.c. si 750V;50Hz pentru circuitele de 24V.c.c.
Tensiunea de incercare se reduce cu20% pentru orice repetare a probei
Se vor respecta instructiunile de protectia muncii de la instalatia de verificat rigiditatea dielectrica
Locul verificarii se imprejmuieste si se semnalizeaza corespunzator.
Proba se efectueaza de personal specializat si autorizat.
Vagon Nr.
Controlor
Data
Se deconecteaza legaturile la DRVC-uri (1e1.1;1e1.2)
1
2
3
4
5
6
7
8
9
10
11
12
13
Pantografe
T
Pant.1a1.1;1a1.2
Caroserie
Deschis,fara sigurantele IT
Comenzile pe 0
T1.1;T1.2
T3
Circ.1 motoare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

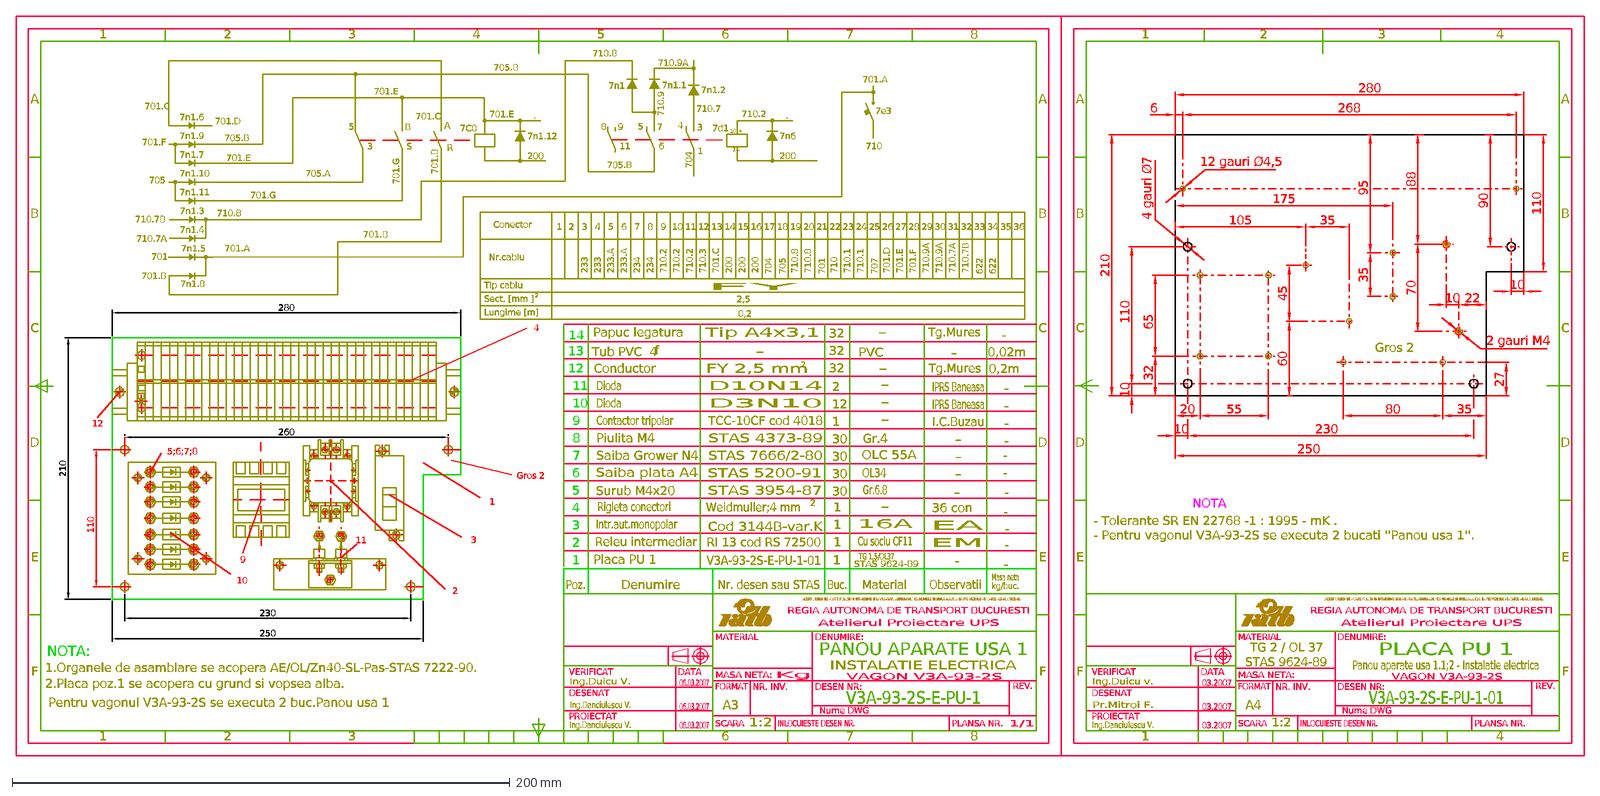
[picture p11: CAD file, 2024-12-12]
PANOURI APARATE/PANOU USA 1.dxf
8
7
6
5
4
3
1
2
F
E
D
C
B
A
Material
PANOU APARATE USA 1
INSTALATIE ELECTRICA
VAGON V3A-93-2S
V3A-93-2S-E-PU-1
Nume DWG
1/1
A3
1:2
Kg
Ing.Duicu V.
06.03.2007
Ing.Danciulescu V.
ACEST DESEN SE POATE FOLOSI IN INTREGIME SAU PE PARTI, ASIGURAND CA NUMELE SI SIGLA R.A.T.B. SA FIE VIZIBILE PE ORICE REPRODUCERE.
PLANSA NR.
REV.
DESEN NR:
INLOCUIESTE DESEN NR.
NR. INV.
SCARA
MASA NETA:
FORMAT
DENUMIRE:
REGIA AUTONOMA DE TRANSPORT BUCURESTI
MATERIAL
PROIECTAT
DESENAT
DATA
VERIFICAT
Atelierul Proiectare UPS
Denumire
Poz.
Nr. desen sau STAS
Buc.
Observatii
Masa neta
kg/buc.
280
210
260
110
230
-
250
16A
Gr.4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

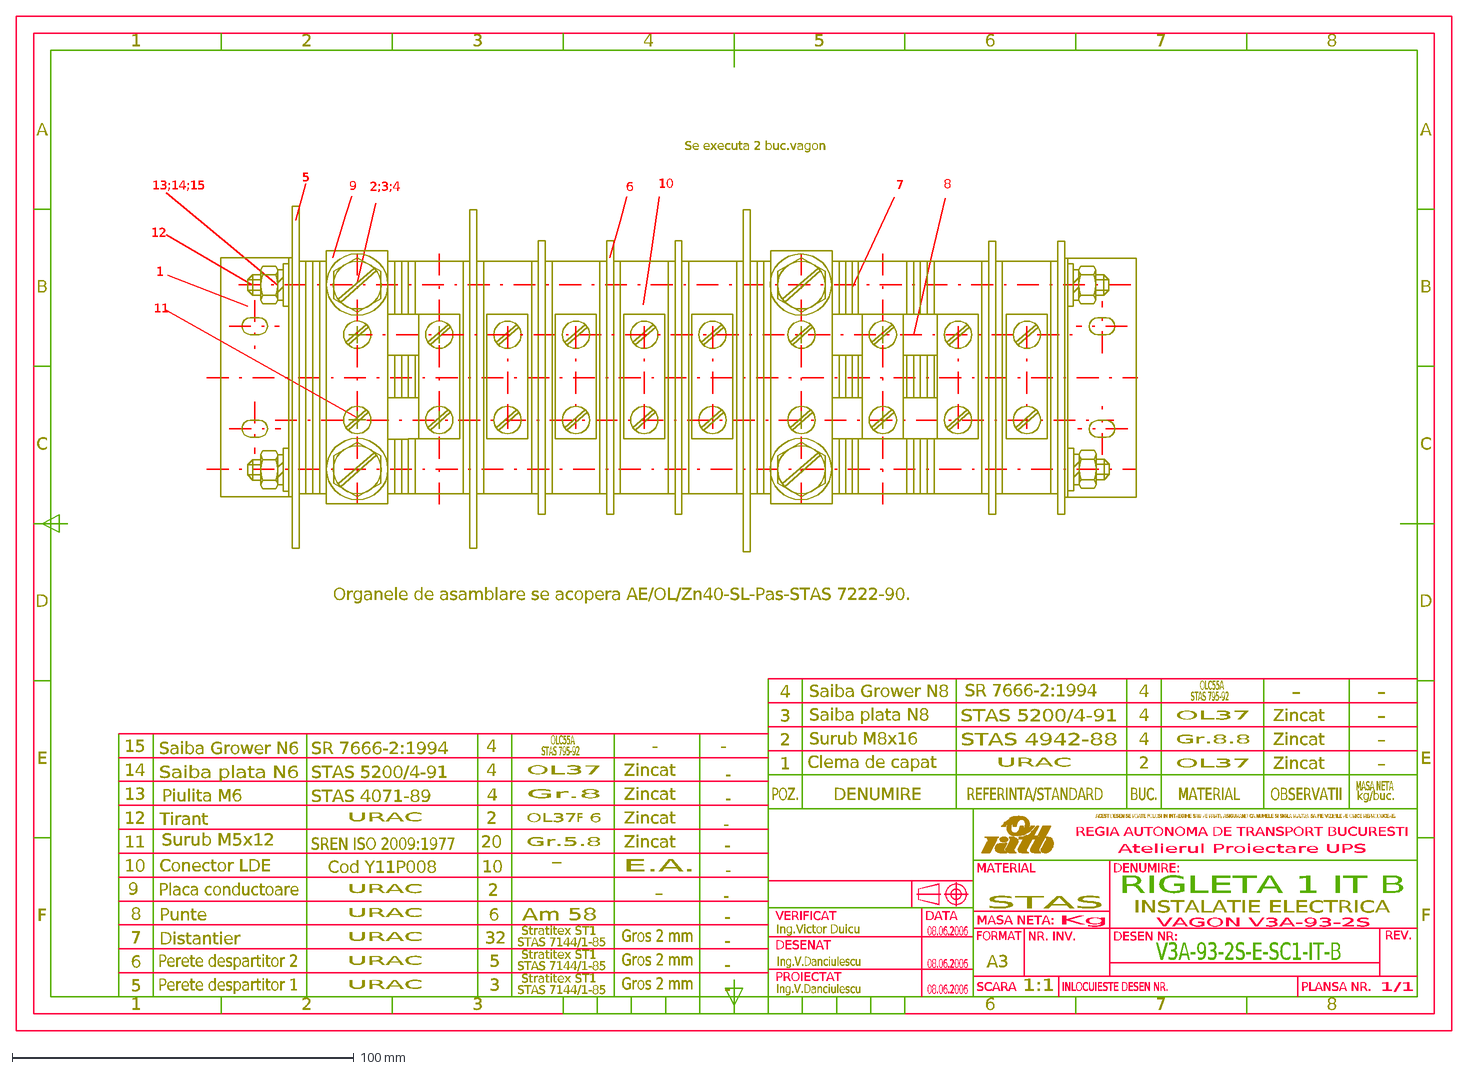
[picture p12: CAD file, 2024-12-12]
SIRURI DE CLEME/RIGLETA 1 IT TRONSON B.dxf
8
7
6
5
4
3
1
2
F
E
D
C
B
A
9
10
32
11
12
14
13
20
BUC.
RIGLETA 1 IT B
INSTALATIE ELECTRICA
VAGON V3A-93-2S
V3A-93-2S-E-SC1-IT-B
1/1
A3
1:1
STAS
Kg
Ing.Victor Duicu
08.06.2006
Ing.V.Danciulescu
ACEST DESEN SE POATE FOLOSI IN INTREGIME SAU PE PARTI, ASIGURAND CA NUMELE SI SIGLA R.A.T.B. SA FIE VIZIBILE PE ORICE REPRODUCERE.
PLANSA NR.
REV.
DESEN NR:
INLOCUIESTE DESEN NR.
NR. INV.
SCARA
MASA NETA:
FORMAT
DENUMIRE:
REGIA AUTONOMA DE TRANSPORT BUCURESTI
MATERIAL
PROIECTAT
DESENAT
DATA
VERIFICAT
Atelierul Proiectare UPS
DENUMIRE
POZ.
REFERINTA/STANDARD
OBSERVATII
kg/buc.
MASA NETA
Organele de asamblare se acopera AE/OL/Zn40-SL-Pas-STAS 7222-90.
Se executa 2 buc.vagon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

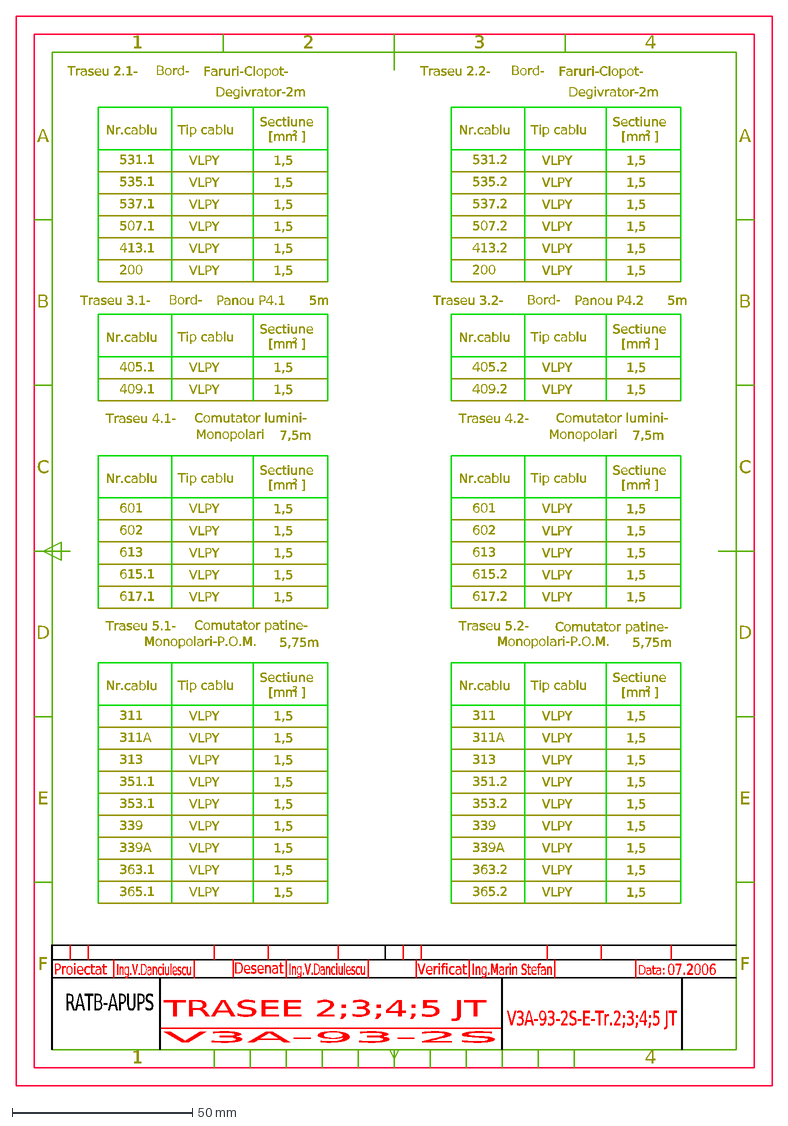
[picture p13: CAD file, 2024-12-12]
TRASEE SI JURNALE DE CABLURI/TRASEE 2;3;4;5 JT.dxf
F
E
D
C
B
A
4
3
2
1
TRASEE 2;3;4;5 JT
V3A-93-2S
V3A-93-2S-E-Tr.2;3;4;5 JT
Ing.V.Danciulescu
Ing.Marin Stefan
07.2006
RATB-APUPS
Proiectat
Verificat
Desenat
Data:
537.1
VLPY
535.1
1,5
Traseu 2.1-
Tip cablu
531.1
Nr.cablu
[mm ]
Sectiune
Faruri-Clopot-
Bord-
Degivrator-2m
537.2
535.2
531.2
Panou P4.1
Traseu 3.1-
409.1
405.1
5m
Panou P4.2
Traseu 3.2-
409.2
405.2
Monopolari
613
Traseu 4.1-
602
601
Comutator lumini-
7,5m
507.1
413.1
413.2
507.2
617.1
615.1
617.2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

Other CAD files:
SCHEME SERVICII AUXILIARE/02-01.dxf
SCHEME/SCHEMA DE SEMNALIZARE.dxf
PANOURI APARATE/PANOU P1.1.dxf
SCHEME/SCHEMA DE AUTOTAXARE.dxf
TRAMVAI V3A-2S.dxf
SCHEME/SCHEMA DE IMPAMANTARE.dxf
BORDEROU DESENE.dwg
FISE DE MASURATORI/FISA DE MASURATORI 2 - ARIAL.dwg
FISE DE MASURATORI/FISA DE MASURATORI 2 - ARIAL.dxf
FISE DE MASURATORI/FISA DE MASURATORI 2.dwg
FISE DE MASURATORI/FISA DE MASURATORI 2.dxf
FISE DE MASURATORI/FISA DE MASURATORI 3 - ARIAL.dwg
FISE DE MASURATORI/FISA DE MASURATORI 3.dwg
FISE DE MASURATORI/FISA DE MASURATORI 4 - ARIAL.dwg
FISE DE MASURATORI/FISA DE MASURATORI 4.dwg
FISE DE MASURATORI/FISA DE MASURATORI 4.dxf
FISE DE MASURATORI/FISA DE MASURATORI 5 - ARIAL.dwg
FISE DE MASURATORI/FISA DE MASURATORI 5 - ARIAL.dxf
FISE DE MASURATORI/FISA DE MASURATORI 5.dwg
FISE DE MASURATORI/FISA DE MASURATORI 5.dxf
PANOURI APARATE/AMENAJARE CUTII APARATE.dwg
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

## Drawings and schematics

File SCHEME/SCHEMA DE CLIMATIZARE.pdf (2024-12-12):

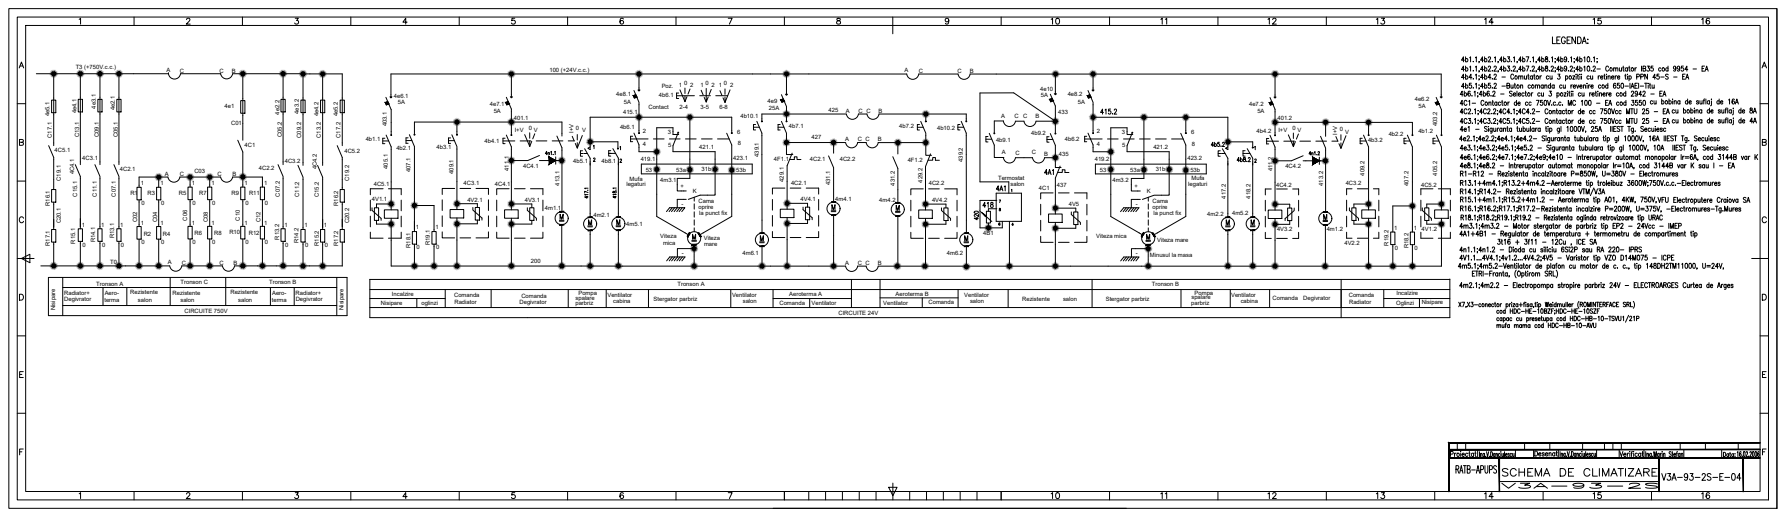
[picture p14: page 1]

A Ventilator CIRCUITE 24V 4C2.2terma Aero- Tronson B

R16.2 4V1.1 4V2.1 4V3.1 Cama 4V4.1 4m1.1 Radiator+ Incalzire Degivrator

C20.2 oglinzi Radiator Comanda Degivrator Comanda

NisipareRadiator+ Degivrator terma Aero-

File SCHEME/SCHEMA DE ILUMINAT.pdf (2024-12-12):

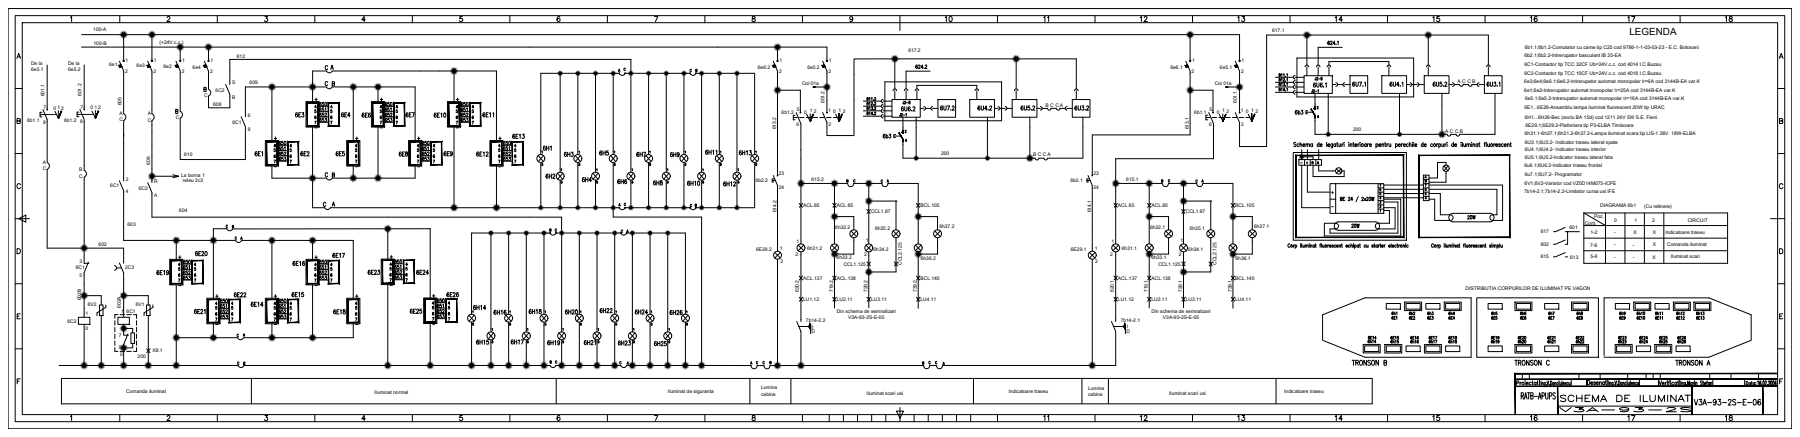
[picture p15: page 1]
Comanda iluminat; Iluminat normal; Iluminat de siguranta; Indicatoare traseu; cabina; Iluminat scari usi; Col 01a 0 5; ACL.138 1; 739.2 CCL2.125; Col 01a 65 0 1 2; 739.1 CCL2.125; (Cu retinere); DISTRIBUTIA CORPURILOR DE ILUMINAT PE VAGON B C C A B C C A; La borna 1 releu 2c3

6b1.1;6b1.2-Comutator cu came tip C25 cod 9786-1-1-03-03-23 - E.C. Botosani
6b2.1;6b2.2-Intrerupator basculant IB 35-EA

6C1-Contactor tip TCC 32CF Ub=24V.c.c. cod 4014 I.C.Buzau
6C2-Contactor tip TCC 10CF Ub=24V.c.c. cod 4018 I.C.Buzau
6e3;6e4;6e6.1;6e6.2-Intrerupator automat monopolar Ir=6A cod 3144B-EA var.K
6e1;6e2-Intrerupator automat monopolar Ir=25A cod 3144B-EA var.K
6e5.1;6e5.2-Intrerupator automat monopolar Ir=16A cod 3144B-EA var.K
6E1...6E26-Ansamblu lampa iluminat fluorescent 20W tip URAC

6H1...6H26-Bec (soclu BA 15d) cod 1211 24V 5W S.E. Fieni
6E29.1;6E29.2-Plafoniera tip P3-ELBA Timisoara
6h31.1-6h37.1;6h31.2-6h37.2-Lampa iluminat scara tip LIS-1 28V. 18W-ELBA
6U3.1;6U3.2- Indicator traseu lateral spate
6U4.1;6U4.2- Indicator traseu interior
6U5.1;6U5.2-Indicator traseu lateral fata
6u6.1;6U6.2-Indicator traseu frontal
6u7.1;6U7.2- Programator

6V1;6V2-Varistor cod VZ0D14M075-ICPE
7b14-2.1;7b14-2.2-Limitator cursa usi IFE

5-6 Poz. | - | -- DIAGRAMA 6b1 | CIRCUIT

Cont. 1-2 | -0- | 1X | Indicatoare traseu

7-8 | | | Comanda iluminat

Iluminat scari

Din schema de semnalizari

Indicatoare traseu Iluminat scari usi

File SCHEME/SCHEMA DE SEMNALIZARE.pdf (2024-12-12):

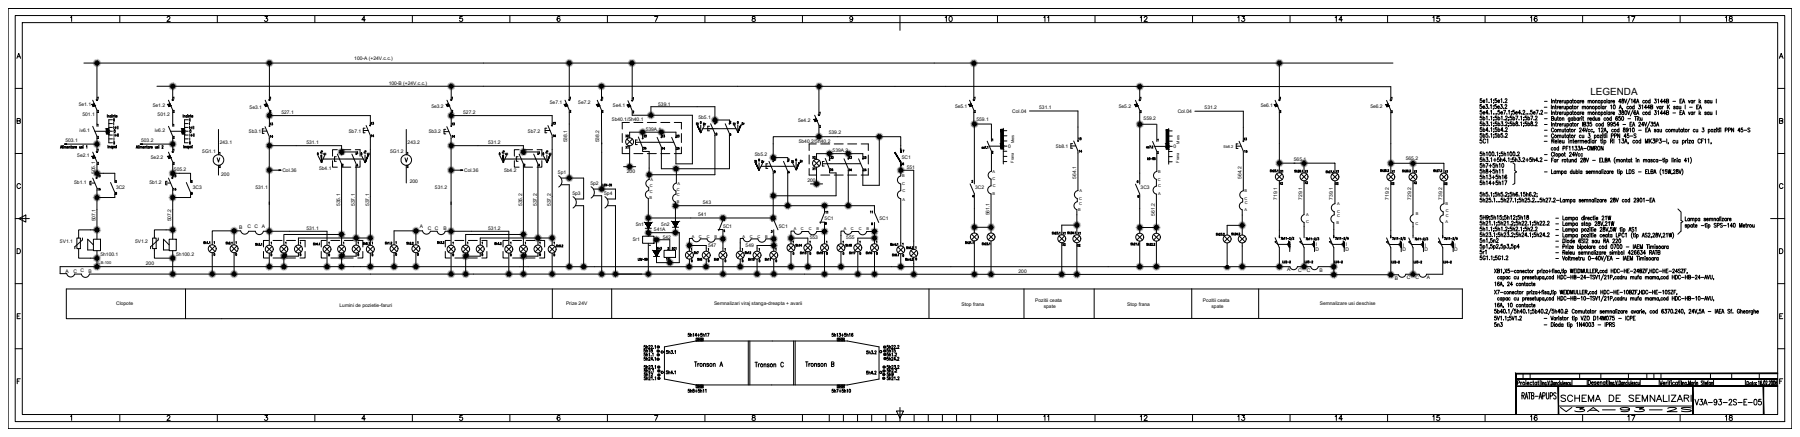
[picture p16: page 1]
C 527.2 Col.36; Clopote LB-100; Lumini de pozietie-faruri 503.15b1.1 5V1.1; 537.1 531.15b4.1 Col.36; Prize 24V; Semnalizari viraj stanga-dreapta + avarii; spate Pozitii ceata Stop frana; Stop frana; Pozitii ceata spate 555 539A.1539.1 541A 5p1; Frana 559.1 5e5.1 Mers Col.04 5b8.1

Mers Col.04 531.2 Semnalizare usi deschise

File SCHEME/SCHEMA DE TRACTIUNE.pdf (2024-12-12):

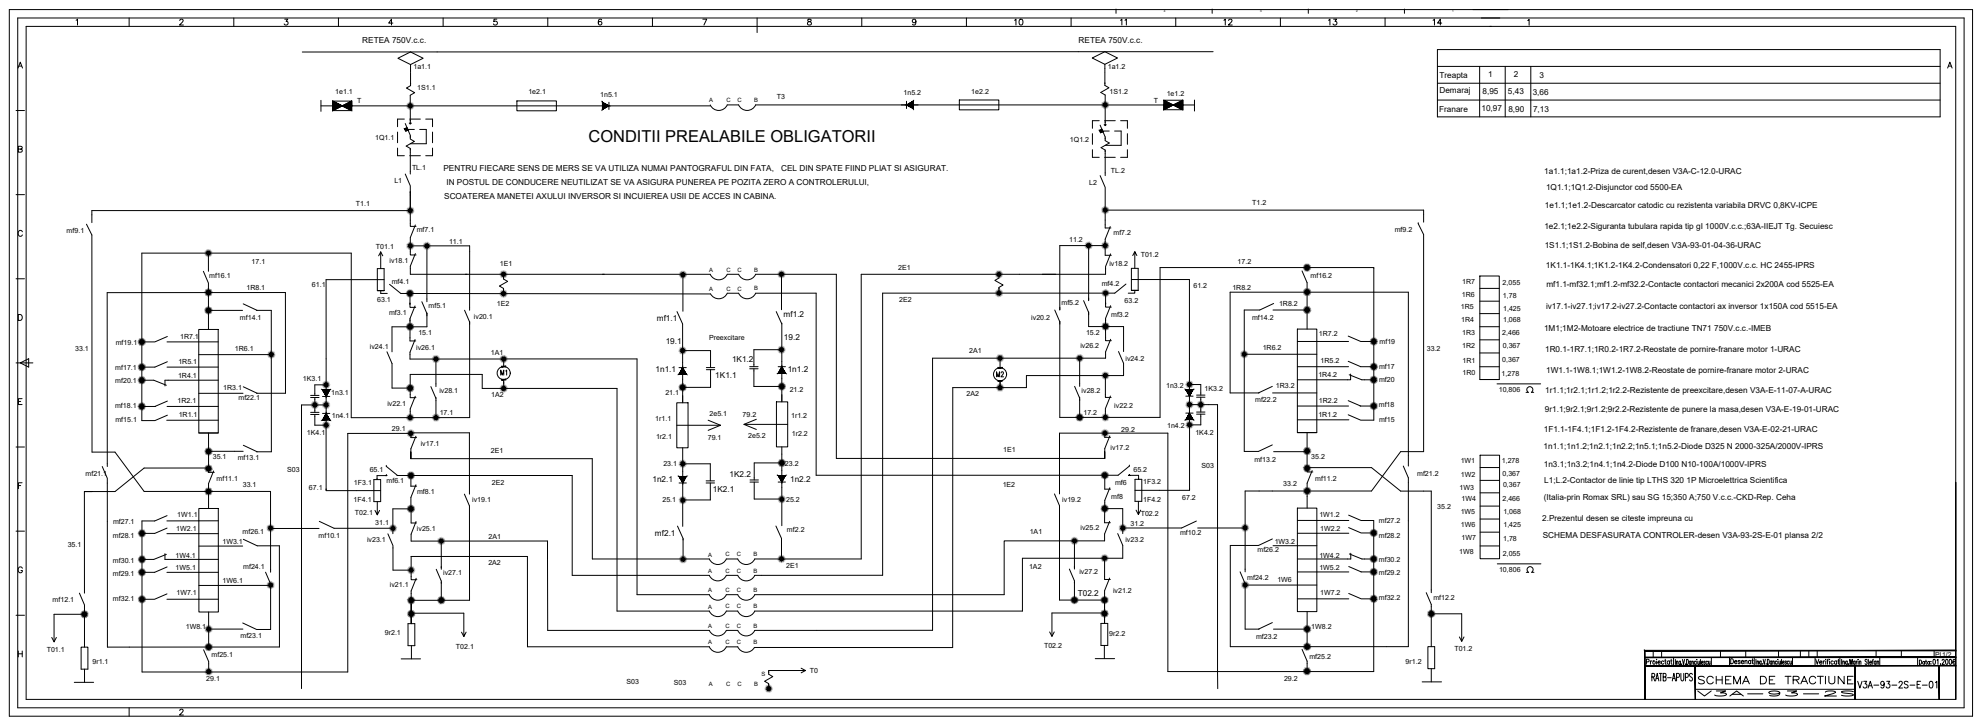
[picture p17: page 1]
IN POSTUL DE CONDUCERE NEUTILIZAT SE VA ASIGURA PUNEREA PE POZITA ZERO A CONTROLERULUI, PENTRU FIECARE SENS DE MERS SE VA UTILIZA NUMAI PANTOGRAFUL DIN FATA, RETEA 750V.c.c. T01.1; BBB A; T0 2E1 mf2.2 SCOATEREA MANETEI AXULUI INVERSOR SI INCUIEREA USII DE ACCES IN CABINA. CEL DIN SPATE FIIND PLIAT SI ASIGURAT. 65.1 67.1; 1K1.2 Preexcitare 1K1.1 A; RETEA 750V.c.c. iv19.2; Franare; 10,97 Demaraj Treapta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

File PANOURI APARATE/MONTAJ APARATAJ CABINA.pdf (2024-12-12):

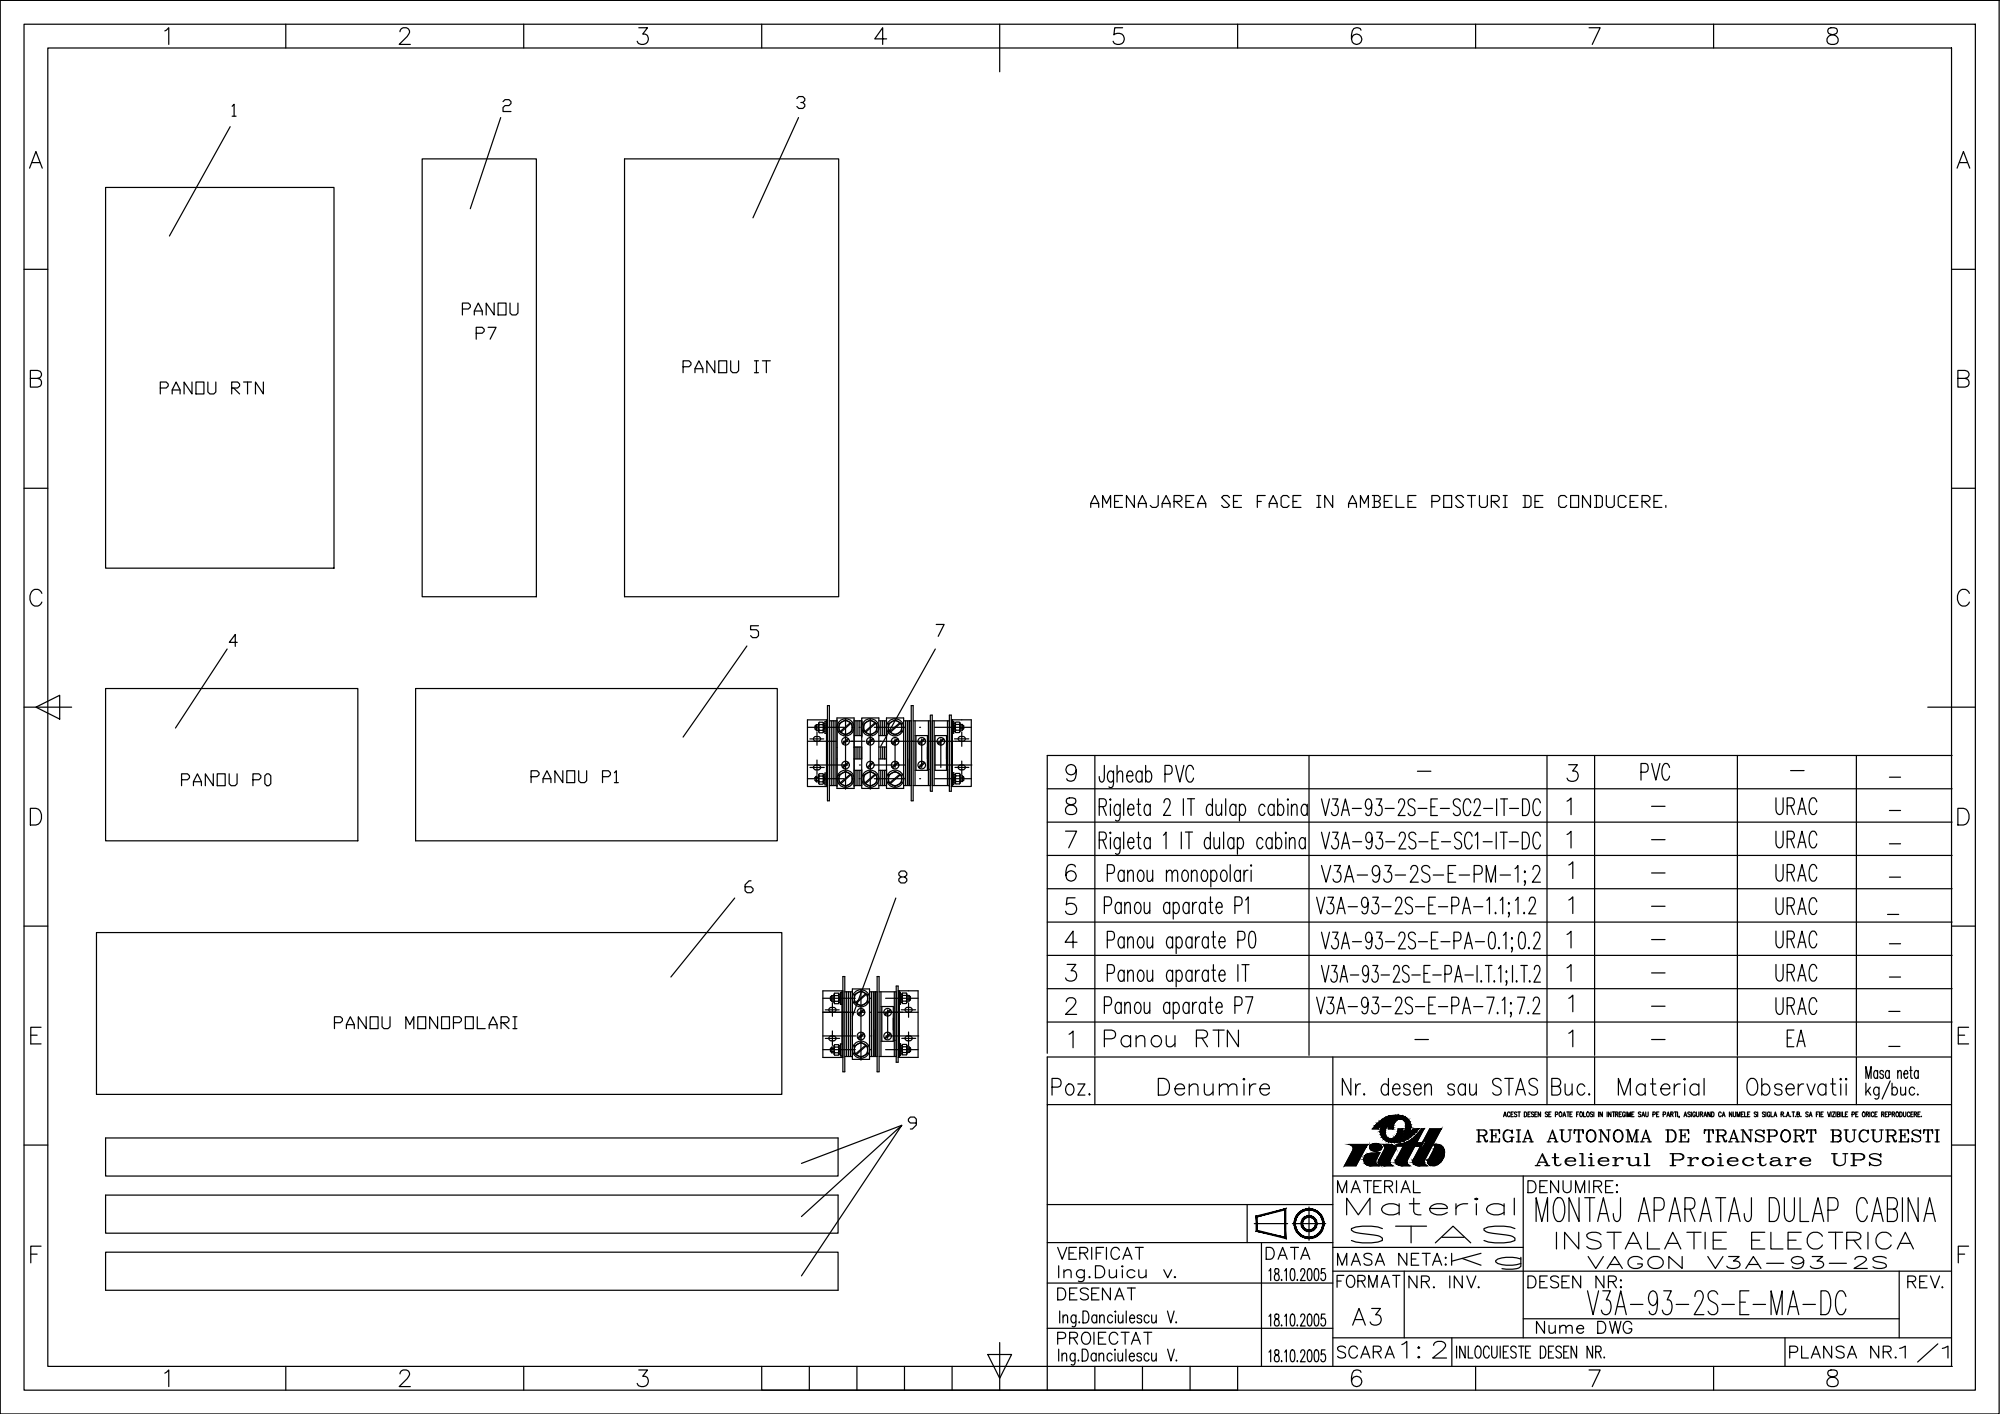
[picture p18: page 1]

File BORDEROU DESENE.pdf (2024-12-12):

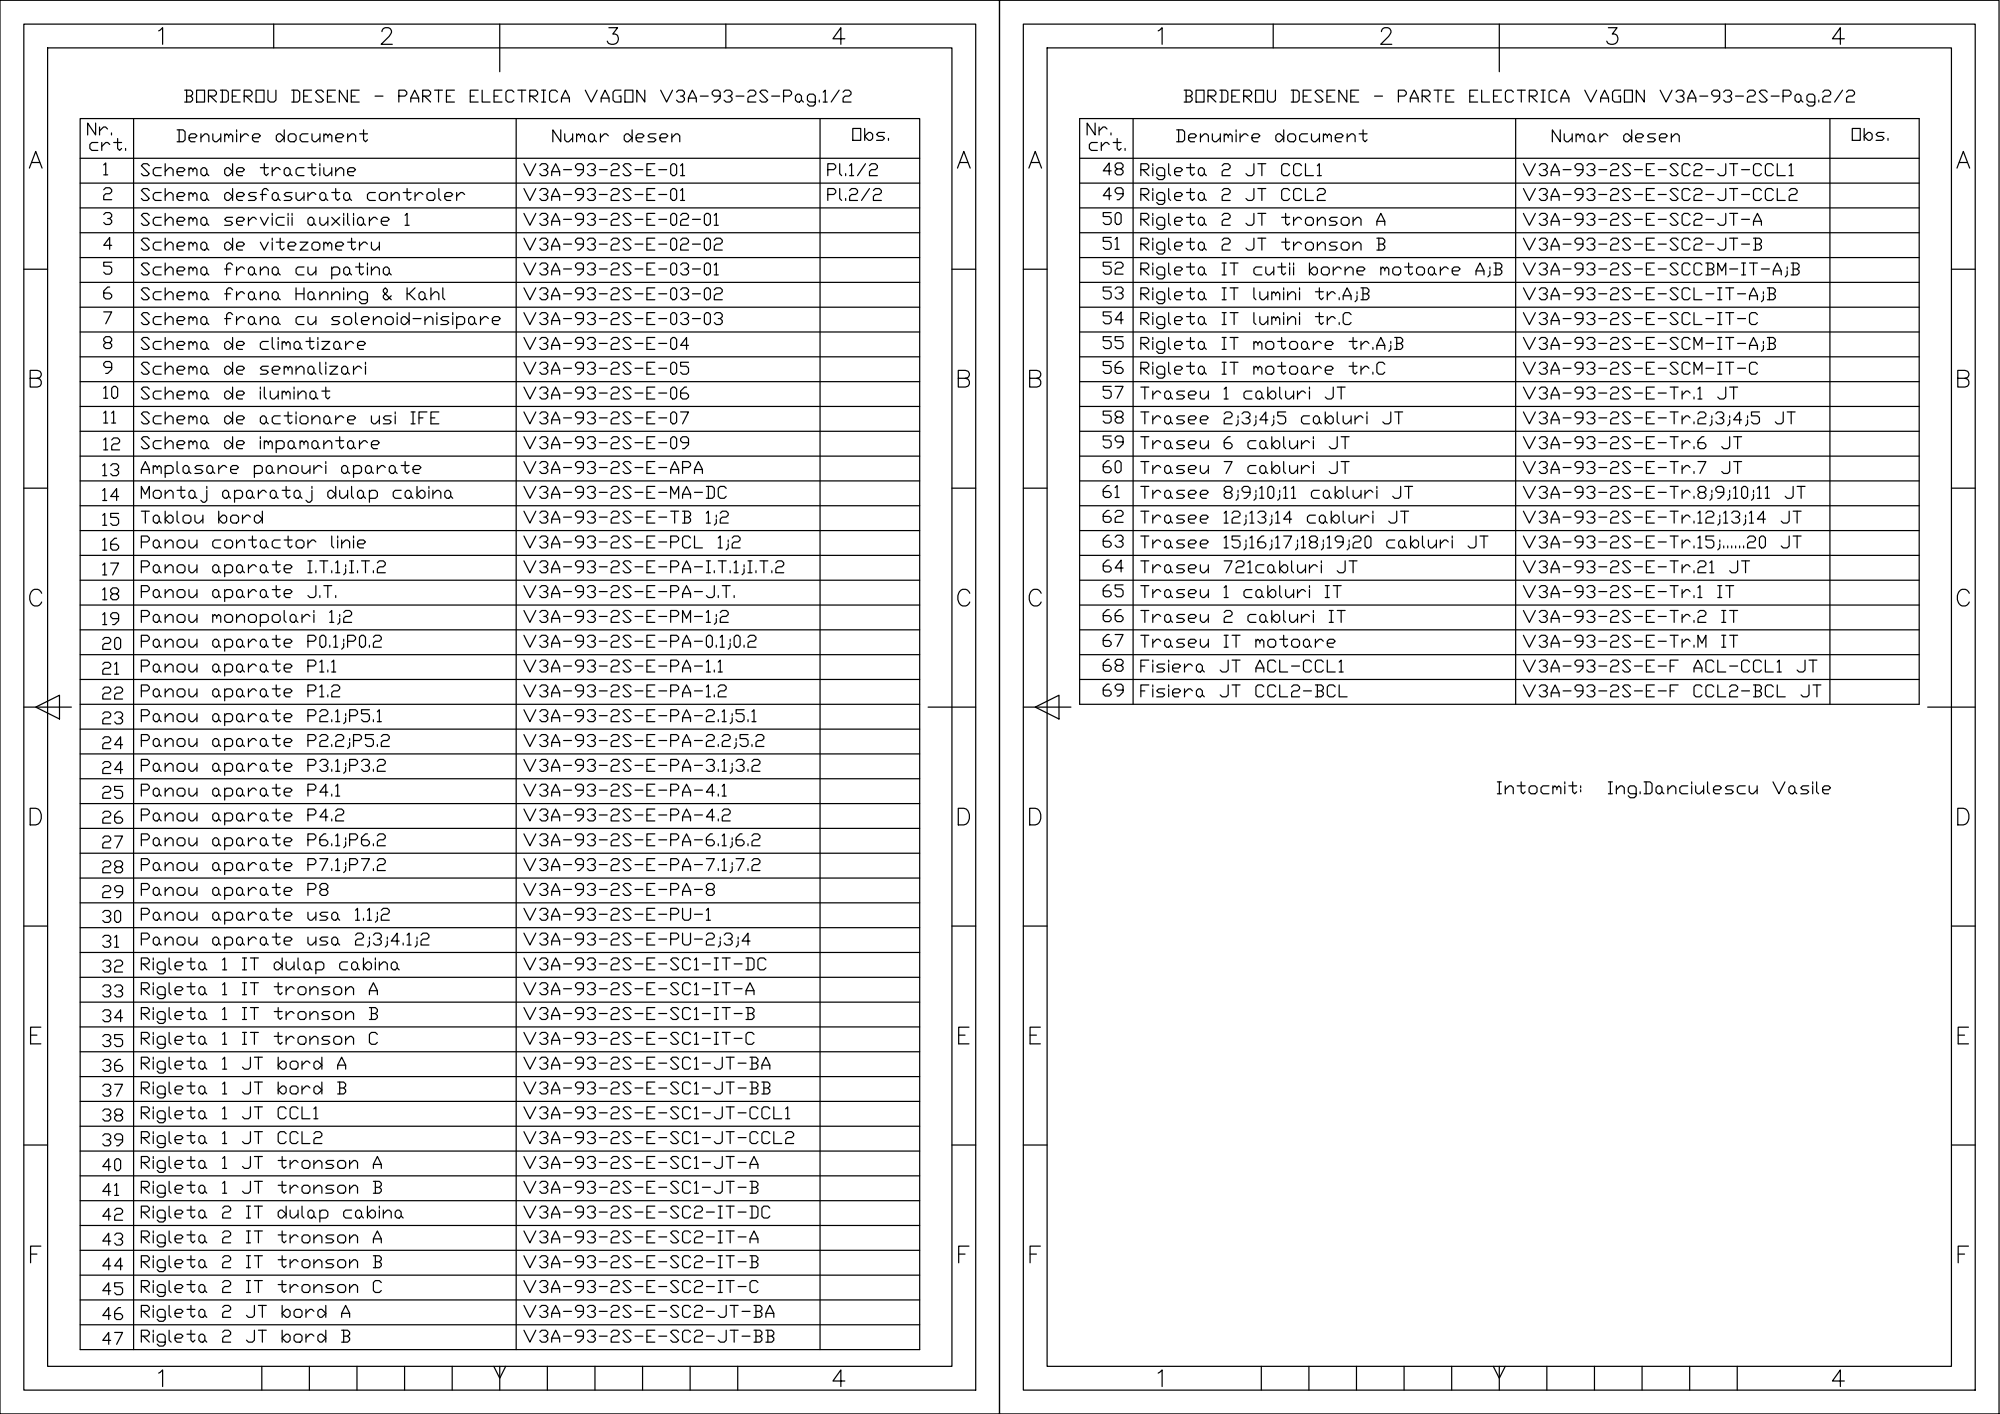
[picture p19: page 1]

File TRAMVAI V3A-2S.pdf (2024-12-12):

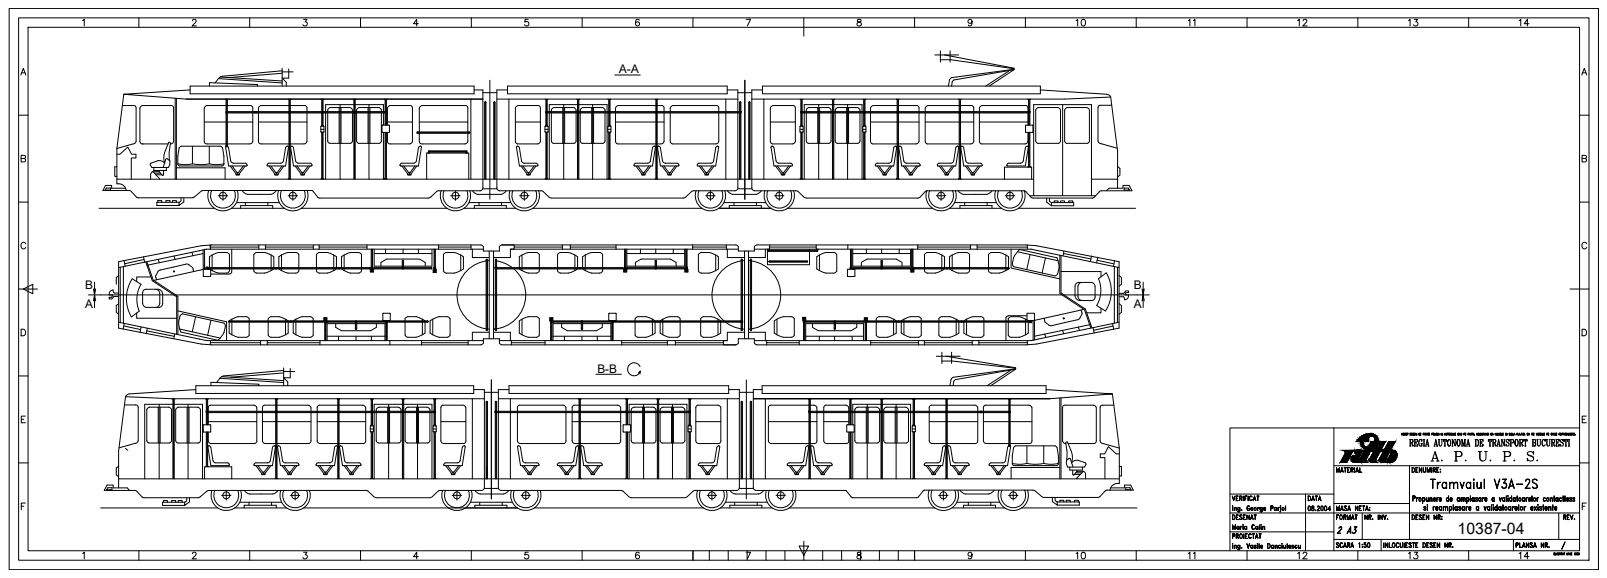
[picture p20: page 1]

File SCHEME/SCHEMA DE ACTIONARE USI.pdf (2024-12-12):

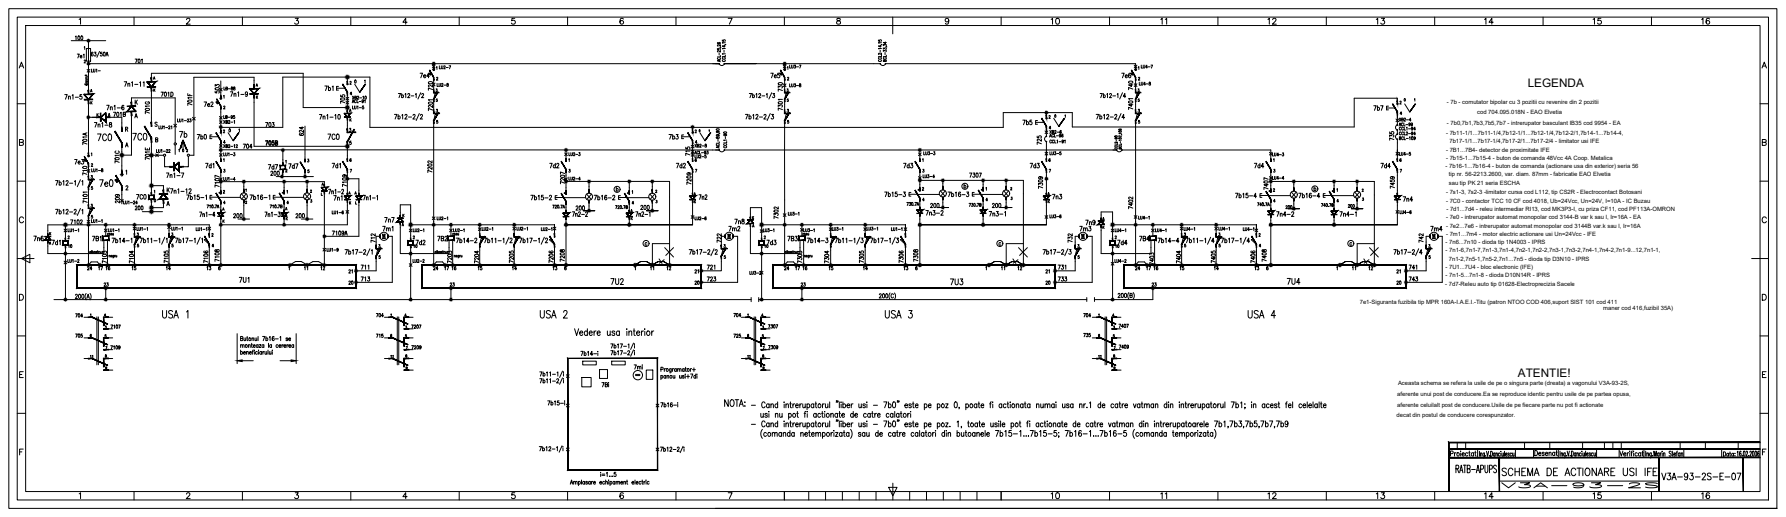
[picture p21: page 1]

Aceasta schema se refera la usile de pe o singura parte (dreata) a vagonului V3A-93-2S, aferente unui post de conducere.Ea se reproduce identic pentru usile de pe partea opusa, aferente celuilalt post de conducere.Usile de pe fiecare parte nu pot fi actionate decat din postul de conducere corespunzator. ATENTIE! LEGENDA 7e1-Siguranta fuzibila tip MPR 160A-I.A.E.I.-Titu (patron NTOO COD 406,suport SIST 101 cod 411 maner cod 416,fuzibil 35A) - 7C0 - contactor TCC 10 CF cod 4018, Ub=24Vcc, Un=24V, I=10A - IC Buzau - 7n1-6,7n1-7,7n1-3,7n1-4,7n2-1,7n2-2,7n3-1,7n3-2,7n4-1,7n4-2,7n1-9...12,7n1-1, - 7b16-1...7b16-4 - buton de comanda (actionare usa din exterior) seria 56 - 7e0 - intrerupator automat monopolar cod 3144-B var k sau l, Ir=16A - EA - 7e2...7e6 - intrerupator automat monopolar cod 3144B var.k sau l, Ir=16A - 7s1-3, 7s2-3 -limitator cursa cod L112, tip CS2R - Electrocontact Botosani - 7d1...7d4 - releu intermediar RI13, cod MK3P3-I, cu priza CF11, cod PF113A-OMRON tip nr. 56-2213.2600, var. diam. 87mm - fabricatie EAO Elvetia - 7b15-1...7b15-4 - buton de comanda 48Vcc 4A Coop. Metalica - 7B1...7B4- detector de proximitate IFE 7b17-1/1...7b17-1/4,7b17-2/1...7b17-2/4 - limitator usi IFE - 7b11-1/1...7b11-1/4,7b12-1/1...7b12-1/4,7b12-2/1,7b14-1...7b14-4, cod 704.095.018N - EAO Elvetia - 7b - comutator bipolar cu 3 pozitii cu revenire din 2 pozitii - 7b0,7b1,7b3,7b5,7b7 - intrerupator basculant IB35 cod 9954 - EA - 7n1-5...7n1-8 - dioda D10N14R - IPRS 7n1-2,7n5-1,7n5-2,7n1...7n5 - dioda tip D3N10 - IPRS - 7n6...7n10 - dioda tip 1N4003 - IPRS - 7m1...7m4 - motor electric actionare usi Un=24Vcc - IFE - 7d7-Releu auto tip 01628-Electroprecizia Sacele sau tip PK 21 seria ESCHA - 7U1...7U4 - bloc electronic (IFE)

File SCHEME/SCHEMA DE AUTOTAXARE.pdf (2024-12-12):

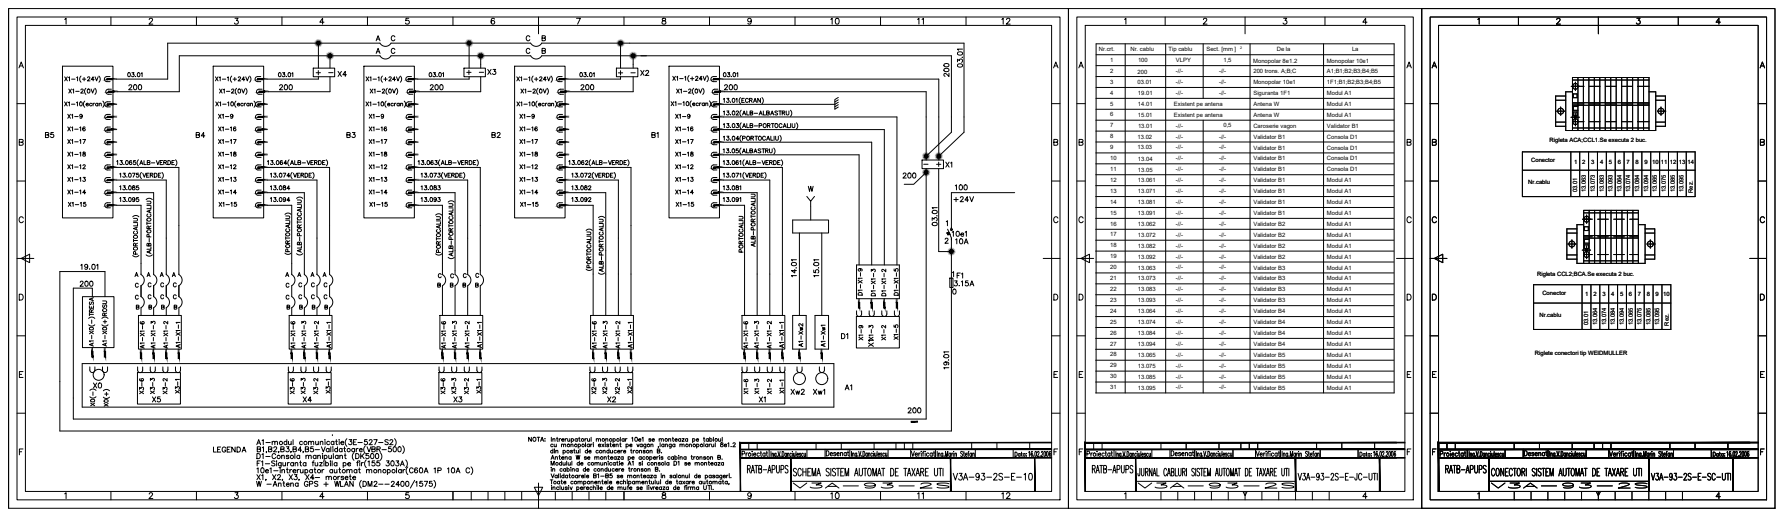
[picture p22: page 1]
Nr.crt.; Nr. cablu; Tip cablu; Sect. [mm ]; 1,5 Existent pe antena Existent pe antena0,5; 200 trons. A;B;C; Monopolar 10e1 A1;B1;B2;B3;B4;B5 Monopolar 10e1; 1F1;B1;B2;B3;B4;B5 Siguranta 1F1; Modul A1 Antena W; Modul A1 Caroserie vagon; Validator B1 Monopolar 8e1.2 Validator B1; Consola D1 Validator B1; Consola D1 Validator B1 Validator B1; Consola D1 Consola D1 Validator B1 Validator B1 Validator B1 Validator B1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

Rez. Rigleta CCL2;BCA.Se executa 2 buc. Conector 1 2 3 4 5 6 7 8 9 10 Riglete conectori tip WEIDMULLER Nr.cablu Conector 1 2 3 4 5 6 7 8 9 10 11 12 13 14Rez. Rigleta ACA;CCL1.Se executa 2 buc. Nr.cablu

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

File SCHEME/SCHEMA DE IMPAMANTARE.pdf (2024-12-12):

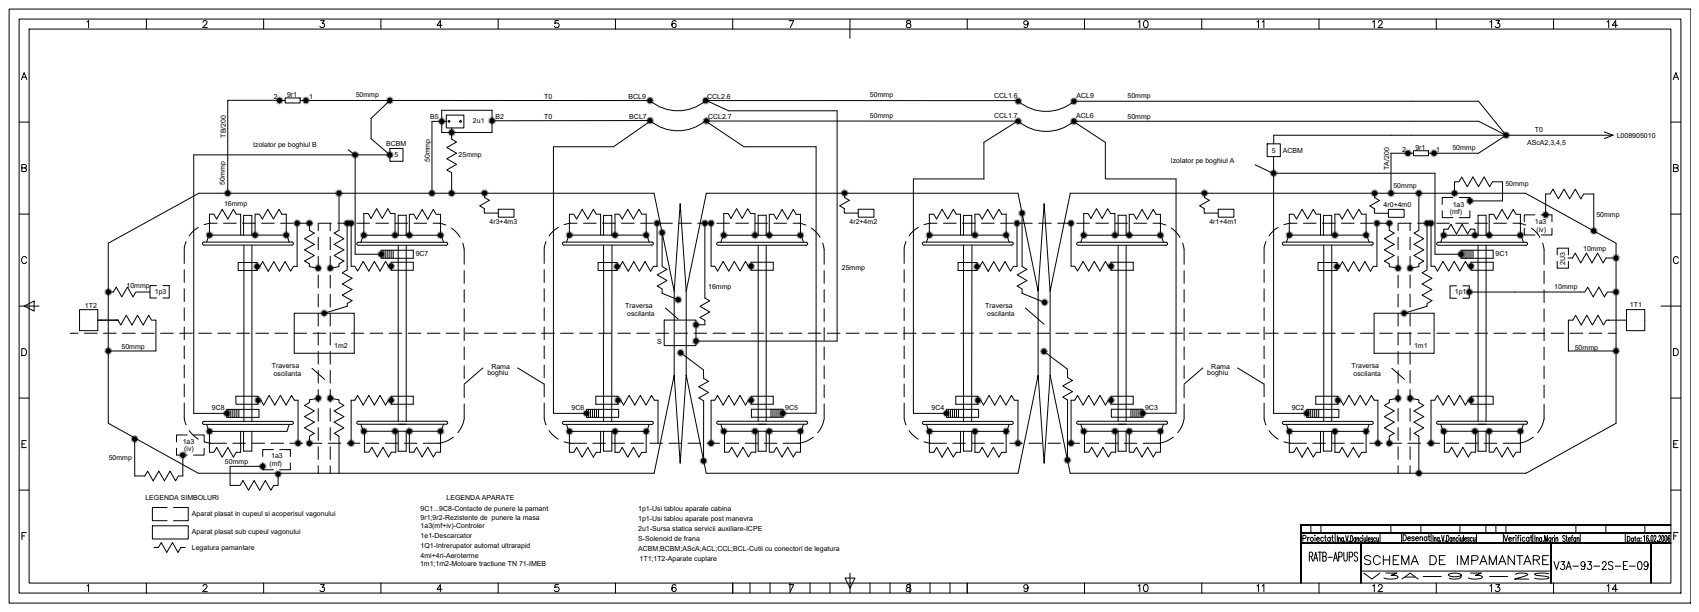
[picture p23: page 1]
Legatura pamantare; LEGENDA SIMBOLURI; 9r1;9r2-Rezistente de punere la masa; 1p1-Usi tablou aparate post manevra; LEGENDA APARATE; 9C7 50mmp 5; 10mmp 2U3

Izolator pe boghiul B TB/200

Izolator pe boghiul A

50mmp

9C1...9C8-Contacte de punere la pamant
1a3(mf+iv)-Controler
1e1-Descarcator
1Q1-Intrerupator automat ultrarapid
4mi+4ri-Aeroterme
1m1;1m2-Motoare tractiune TN 71-IMEB

1p1-Usi tablou aparate cabina

Aparat plasat in cupeul si acoperisul vagonului

2u1-Sursa statica servicii auxiliare-ICPE
S-Solenoid de frana
ACBM;BCBM;AScA;ACL;CCL;BCL-Cutii cu conectori de legatura
1T1;1T2-Aparate cuplare

Aparat plasat sub cupeul vagonului

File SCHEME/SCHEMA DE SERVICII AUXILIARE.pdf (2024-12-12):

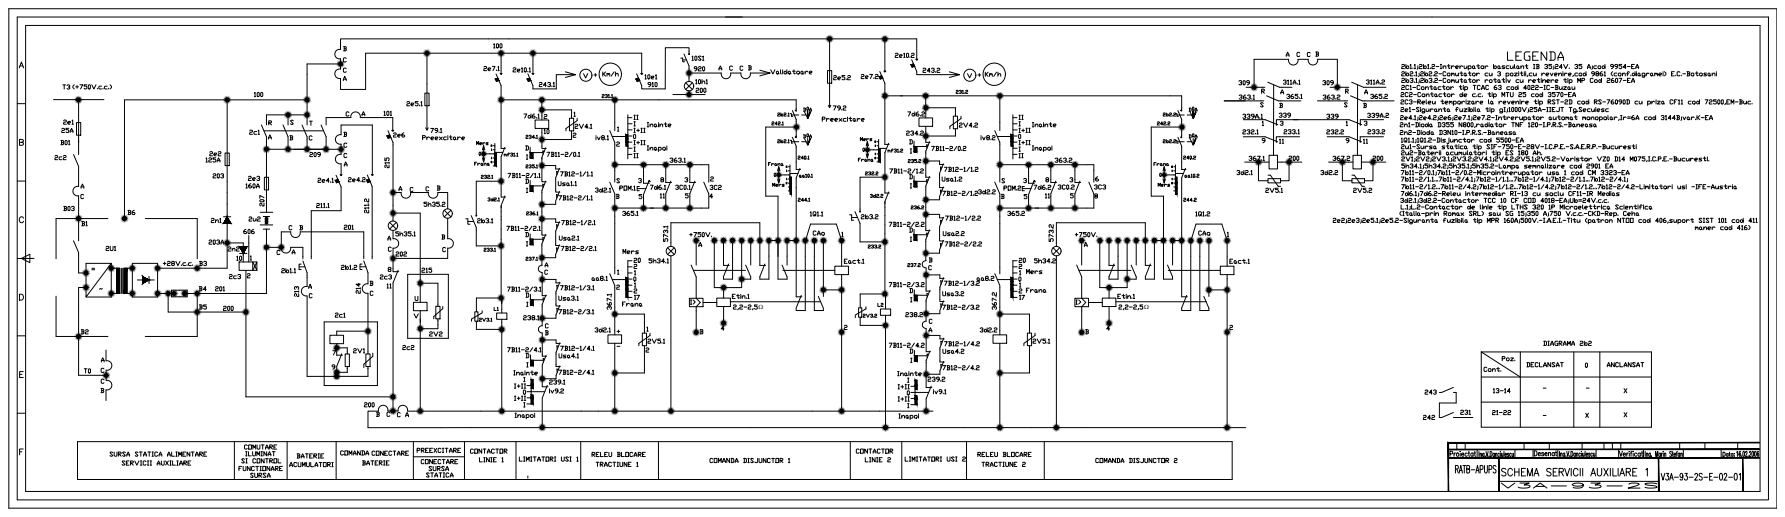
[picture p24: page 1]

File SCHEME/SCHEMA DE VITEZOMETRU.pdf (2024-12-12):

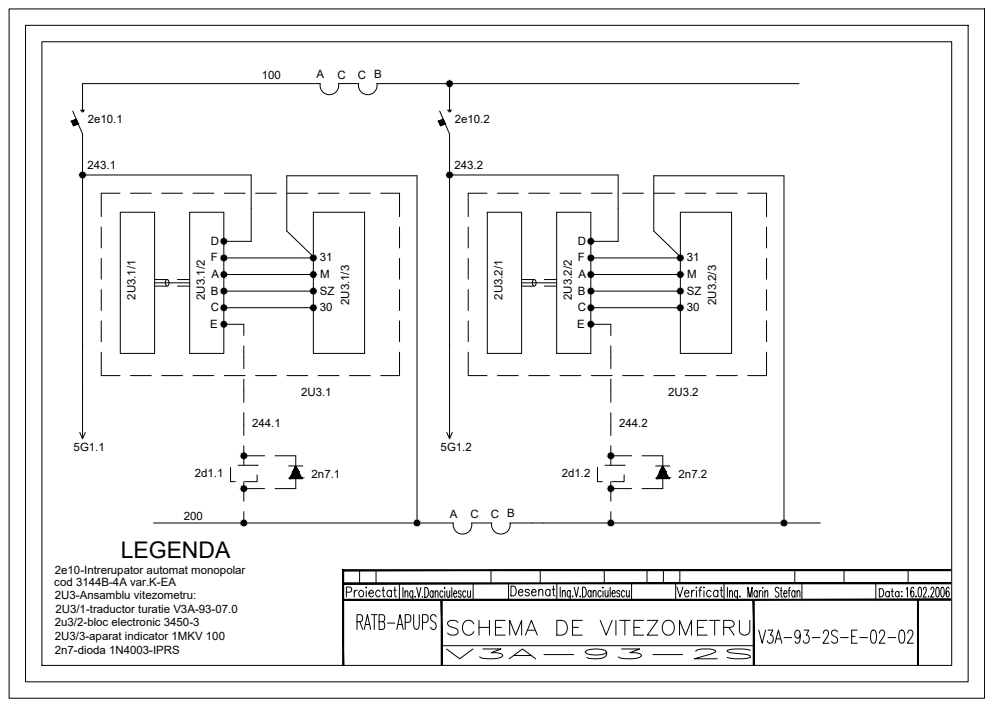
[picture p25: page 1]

2e10-Intrerupator automat monopolar
cod 3144B-4A var.K-EA
2U3-Ansamblu vitezometru:
2U3/1-traductor turatie V3A-93-07.0
2u3/2-bloc electronic 3450-3
2U3/3-aparat indicator 1MKV 100
2n7-dioda 1N4003-IPRS

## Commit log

2024-12-12 Adaugă scheme originale tramvai V3A-2S
    [TRAMVAI V3A-2S.dwg, TRAMVAI V3A-2S.dxf]
2024-12-12 Adaugă borderou desene
    [BORDEROU DESENE.dwg, BORDEROU DESENE.dxf]
2024-12-12 Adaugă fișele de măsurători
    [FISA DE MASURATORI 2 - ARIAL.dwg, FISA DE MASURATORI 2 - ARIAL.dxf, FISA DE MASURATORI 2.dwg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]
2024-12-12 Adaugă panouri aparate
    [AMENAJARE CUTII APARATE.dwg, AMPLASAMENT PANOURI APARATE.dwg, AMPLASAMENT PANOURI APARATE.dxf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]
2024-12-12 Adaugă scheme servicii auxiliare
    [02-01.dwg, 02-01.dxf]
2024-12-12 Adaugă șirurile de cleme
    [RIGLETA 1 IT DULAP CABINA.dwg, RIGLETA 1 IT DULAP CABINA.dxf, RIGLETA 1 IT TRONSON A.dwg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]
2024-12-12 Adaugă traseele de cabluri
    [FISIERA ACL-CCL1 JT.dwg, FISIERA ACL-CCL1 JT.dxf, FISIERA CCL2-BCL JT.dwg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]
2024-12-12 Adaugă schemele tramvaiului
    [SCHEMA DE ACTIONARE USI.dwg, SCHEMA DE ACTIONARE USI.dxf, SCHEMA DE AUTOTAXARE.dwg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]
2024-12-12 Redenumire dosare
    [SCHEMA DE ACTIONARE USI.dwg, SCHEMA DE ACTIONARE USI.dxf, SCHEMA DE AUTOTAXARE.dwg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]
